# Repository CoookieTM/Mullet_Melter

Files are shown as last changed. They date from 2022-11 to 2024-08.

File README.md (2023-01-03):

# Mullet Melter (in ALPHA)

**What is the MulletMelter?**

business in the front, business in the back, party on the sides

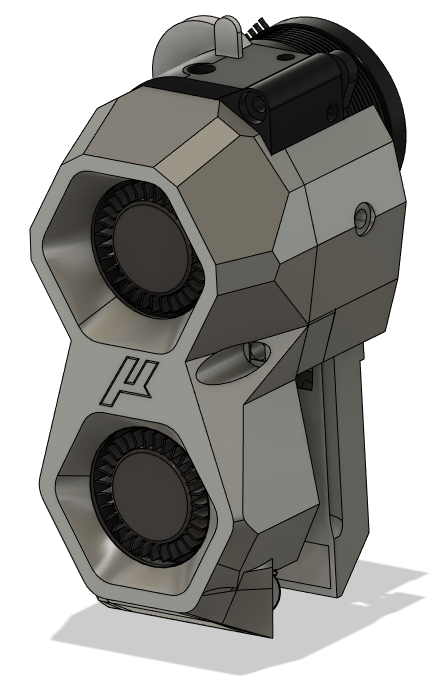
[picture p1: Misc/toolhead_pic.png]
Rendering Mullet Melter




[Join the Doomcube Discord for support under doomy-worx/Mullet_Melter](https://discord.com/channels/825469421346226226/1028744277393674290)

**Requires (3) 3010 Blower Fans**

I have 160hrs of print time on this toolhead so far. (recent toy drive haha)

<details>
    <summary>
    Hardware Required
    </summary>

Part           |Qty | Notes
 ----|----|----|
3010 Blower Fan|3 | 
m3x6		   |5 | 
m3x10 		   |4 | 
m3x10 BHCS     |2 | Must be BHCS
m3x12          |2 |
m3x8           |1 |
heatset inserts|3 |
LGx Lite       |1 |
Revo Voron     |1 |
</details>

Thanks to the following people on Discord who have helped test pre-alpha:

- @Dentox_
- @bwnance

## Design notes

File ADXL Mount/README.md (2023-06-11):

Hardware Required

Part           |Qty | Notes
 ----|----|----|
m3x30		   |1 | 
m3x40 		   |1 | 
heatset inserts|2 |
</details>

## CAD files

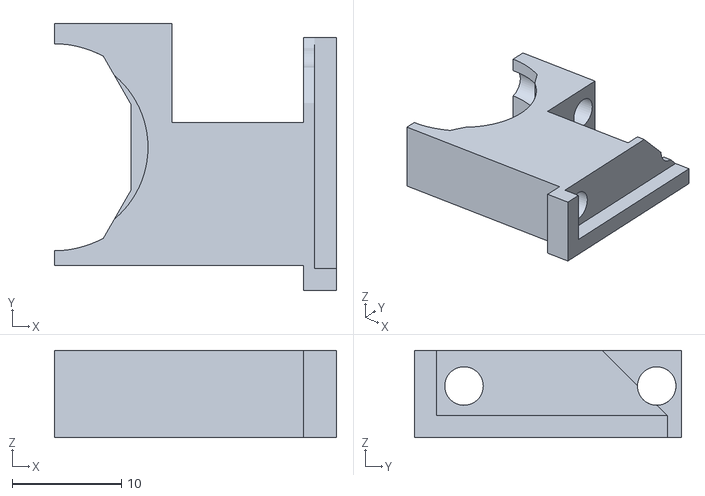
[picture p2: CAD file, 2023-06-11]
ADXL Mount/adxlmount_a.stl
25.8 x 24.4 x 7.99

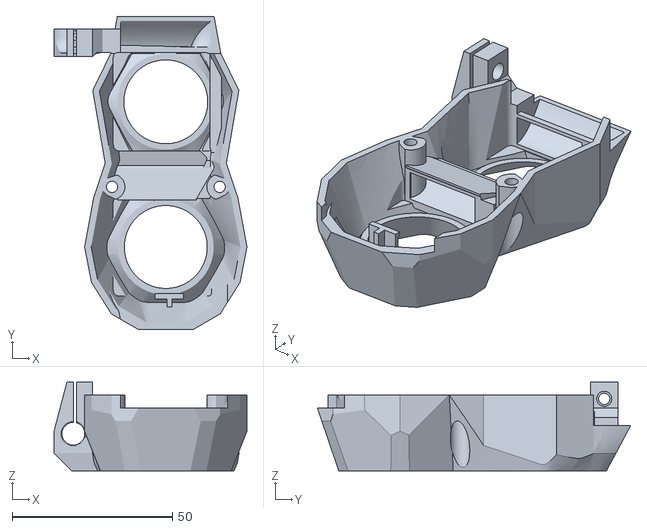
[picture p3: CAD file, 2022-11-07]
Pinda/shroud.stl
60.1 x 97.6 x 27.6

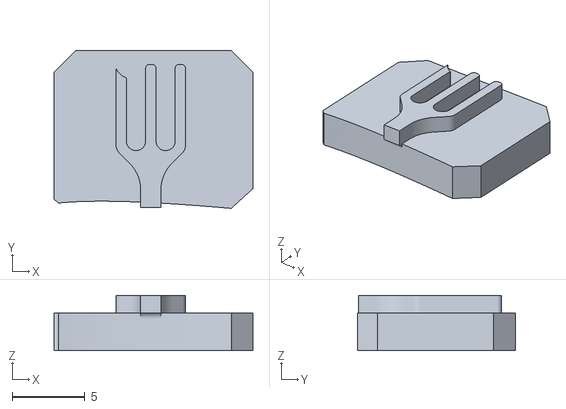
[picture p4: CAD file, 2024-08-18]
Standard/salad_fork/salad_fork_diffuser.stl
13.7 x 10.8 x 3.80

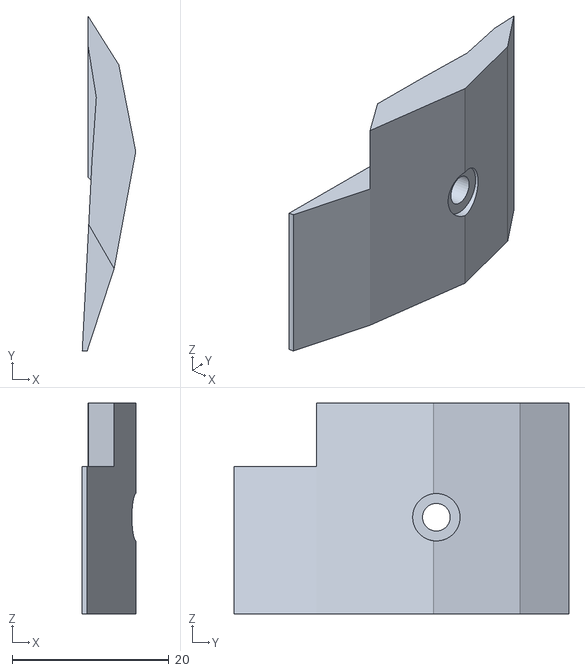
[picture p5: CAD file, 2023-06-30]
Standard/wire_cover.stl
6.83 x 42.8 x 26.9

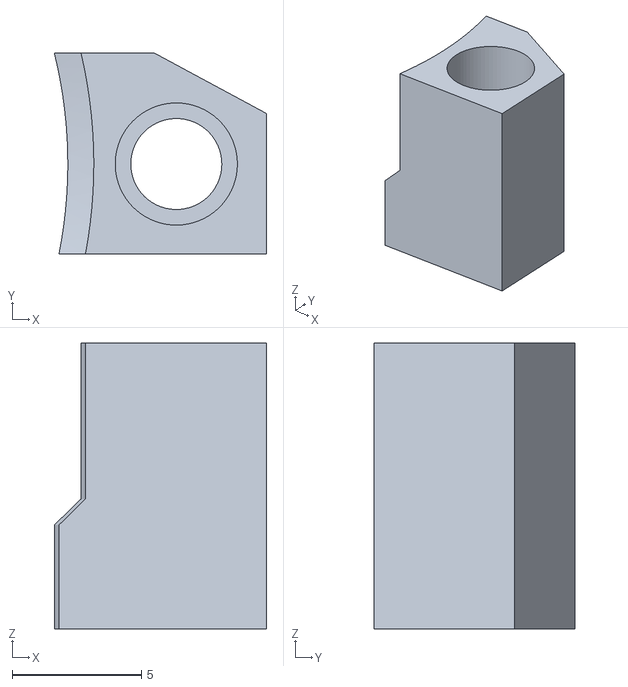
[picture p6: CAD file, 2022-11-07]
Toolhead_Board_Mount/DFH/dfh_coupler_a.stl
8.21 x 7.77 x 11.1

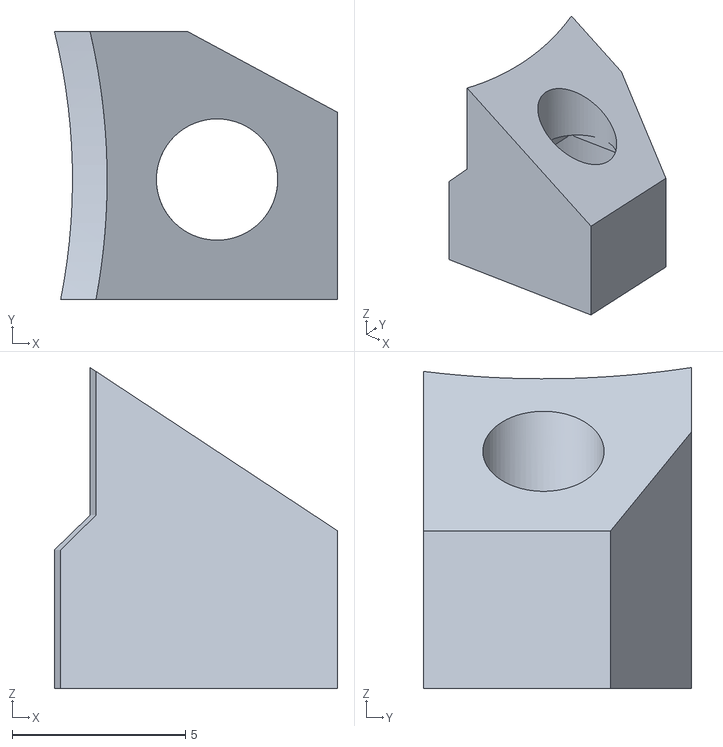
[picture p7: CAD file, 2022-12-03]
Toolhead_Board_Mount/EBB36/coupler_c.stl
8.17 x 7.73 x 9.26

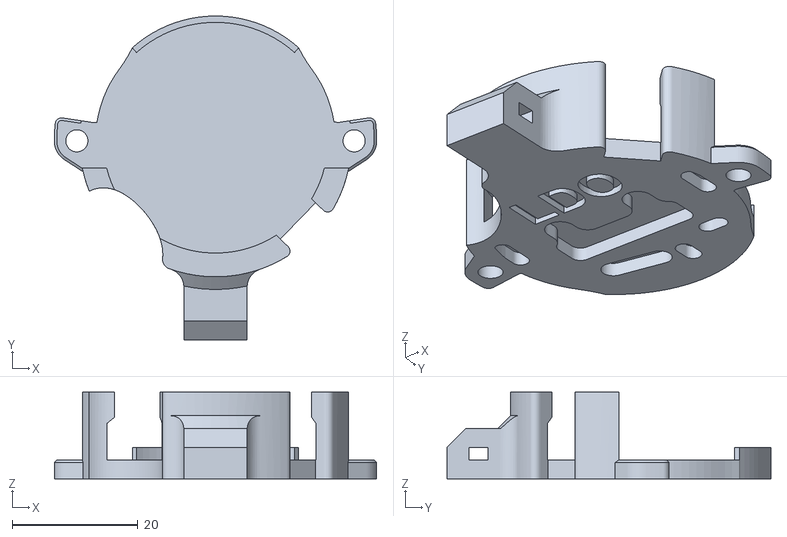
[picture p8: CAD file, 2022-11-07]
Toolhead_Board_Mount/LDO/ldo_backplate.stl
51.3 x 51.5 x 13.8

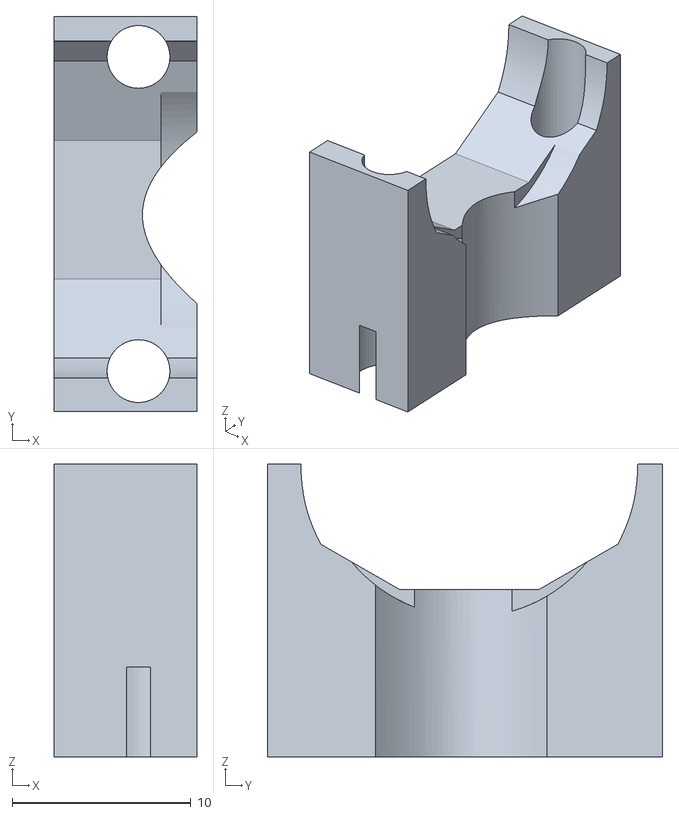
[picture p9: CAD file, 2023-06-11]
ADXL Mount/adxlmount_b.stl
7.99 x 22.1 x 16.4

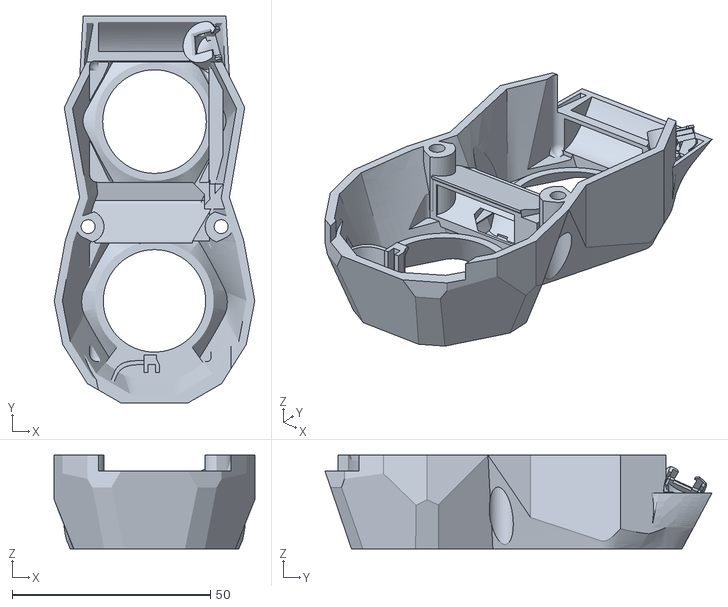
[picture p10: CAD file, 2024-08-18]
Standard/salad_fork/shroud_salad_fork.stl
50.6 x 97.6 x 23.6

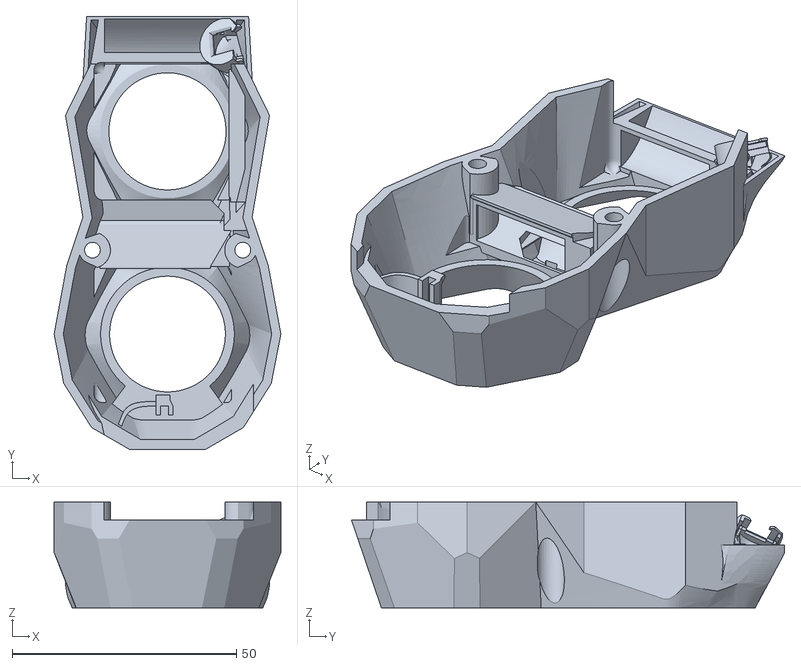
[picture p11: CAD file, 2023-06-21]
Standard/shroud.stl
50.6 x 96.6 x 23.6

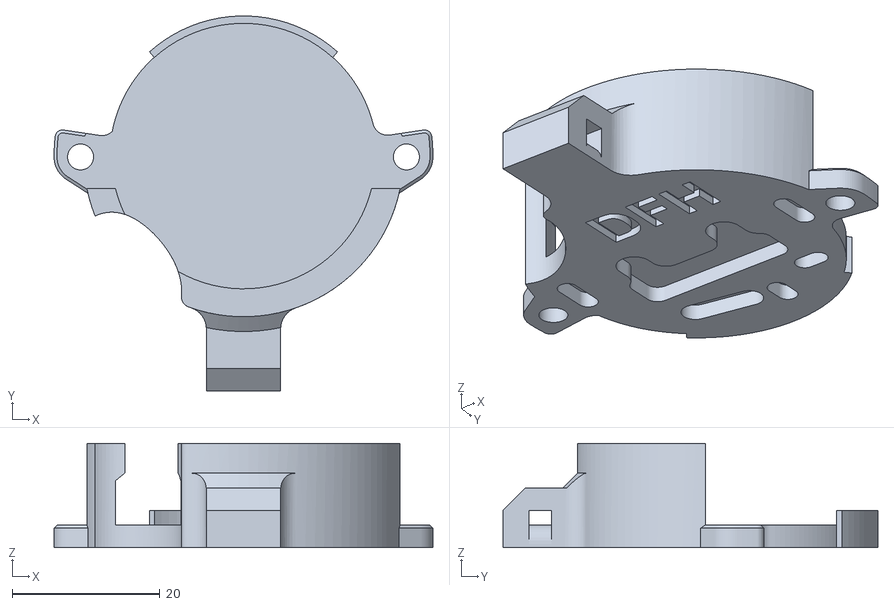
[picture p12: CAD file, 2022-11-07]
Toolhead_Board_Mount/DFH/dfh_backplate.stl
51.3 x 50.7 x 14.1

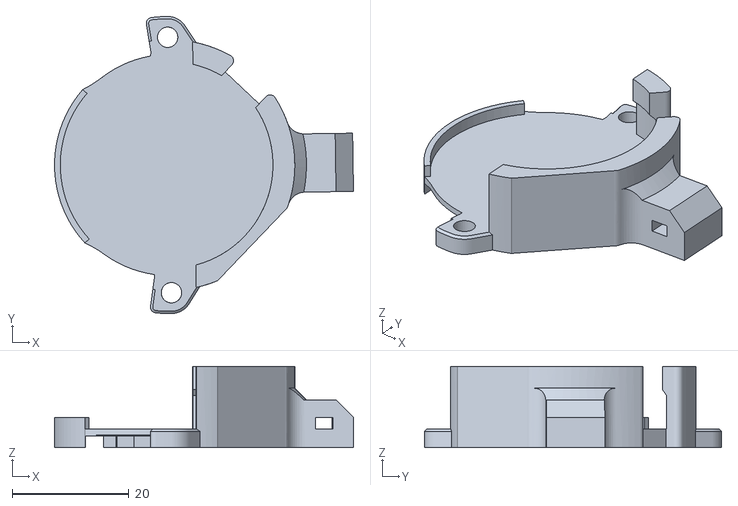
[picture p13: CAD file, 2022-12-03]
Toolhead_Board_Mount/EBB36/backplate.stl
51.3 x 51.0 x 14.0

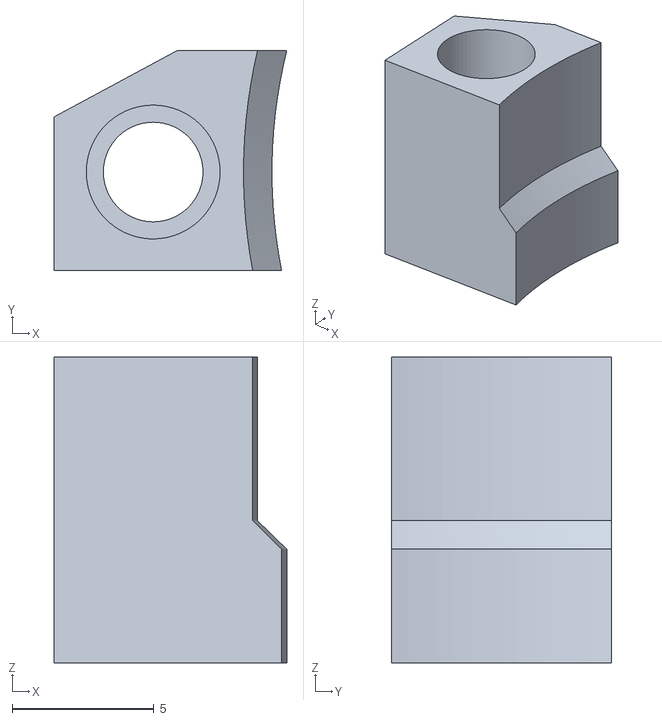
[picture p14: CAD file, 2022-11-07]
Toolhead_Board_Mount/LDO/ldo_coupler_b.stl
8.21 x 7.77 x 10.8

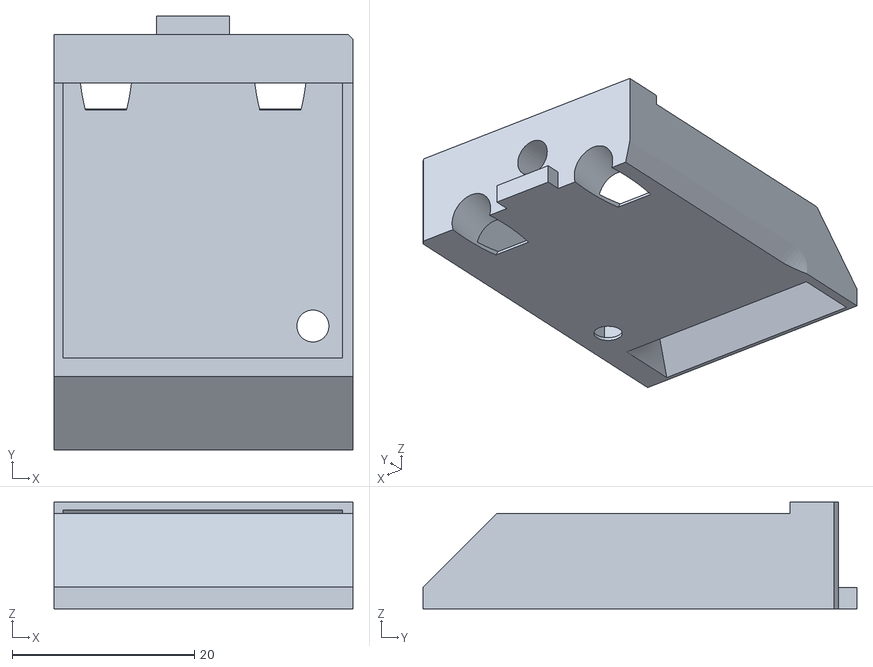
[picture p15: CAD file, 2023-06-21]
Standard/rear_fan_mount.stl
32.8 x 47.5 x 11.7

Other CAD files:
Toolhead_Board_Mount/DFH/dfh_coupler_b.stl
Toolhead_Board_Mount/EBB36/coupler_b.stl
Toolhead_Board_Mount/LDO/ldo_coupler_a.stl
Standard/micron_diffuser.stl
Standard/diffuser_holder.stl
Standard/rail_mount.stl
Toolhead_Board_Mount/EBB36/coupler_a.stl
Toolhead_Board_Mount/EBB36/coupler_d.stl

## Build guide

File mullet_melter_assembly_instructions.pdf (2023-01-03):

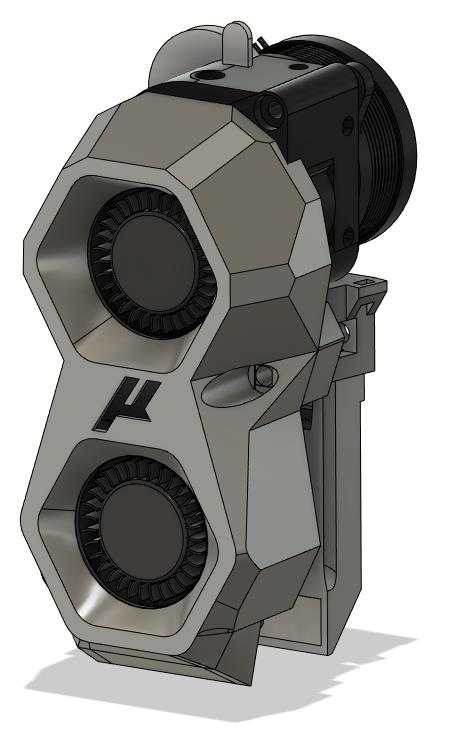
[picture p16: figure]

# Mullet Melter Assembly

### Required:

(3) 3010 Blower Fans (DFH) (https://dfh.fm/products/3010-24v-dual-ball-blower-fan?aff=3) (West3d) (https://west3d.com/products/gdstime-dc-24v-30x30x10-centrifugal-blower-fan-gdb3010-dual-ball-bearing-9500rpm-1w-05a-xh2-54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)

### LGX Lite Revo Voron or Rapido

(5) m3x6
(4) m3x10
(2) m3x10 BHCS
(2) m3x12
(1) m3x8

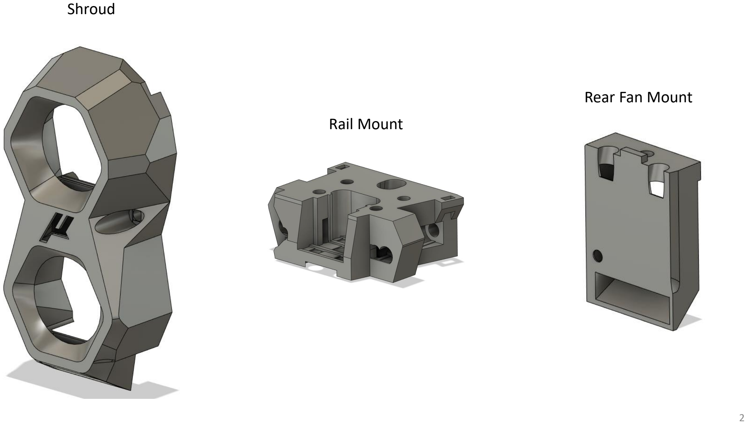
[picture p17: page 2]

Shroud

Rail Mount

Rear Fan Mount

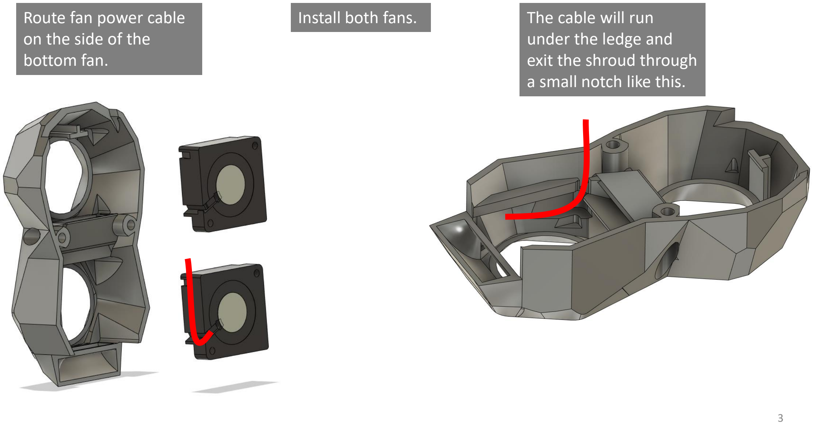
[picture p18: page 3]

Route fan power cable
on the side of the
bottom fan.

The cable will run
under the ledge and
exit the shroud through
a small notch like this.

Install both fans.

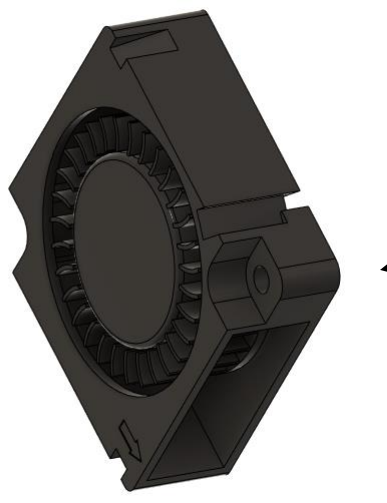
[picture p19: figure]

Use an m3x6 bolt to
pre thread this hole in
the 3010 blower.

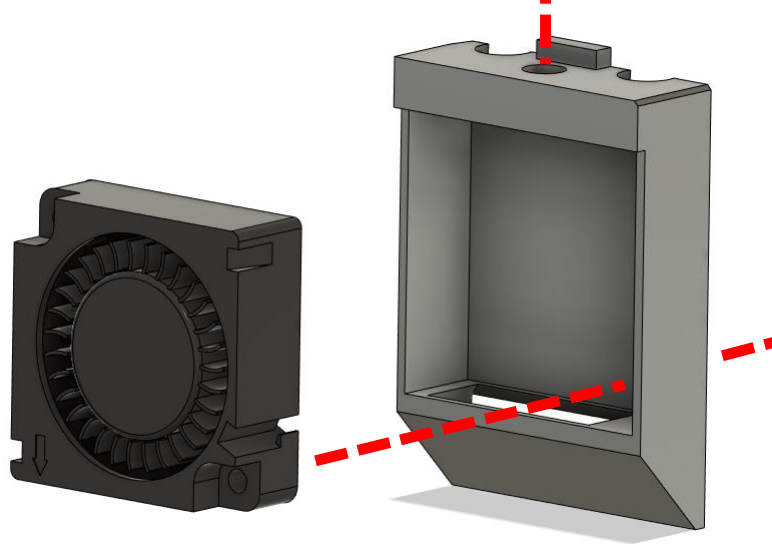
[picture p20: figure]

Remove bolt and reinstall into the rear fan
mount.

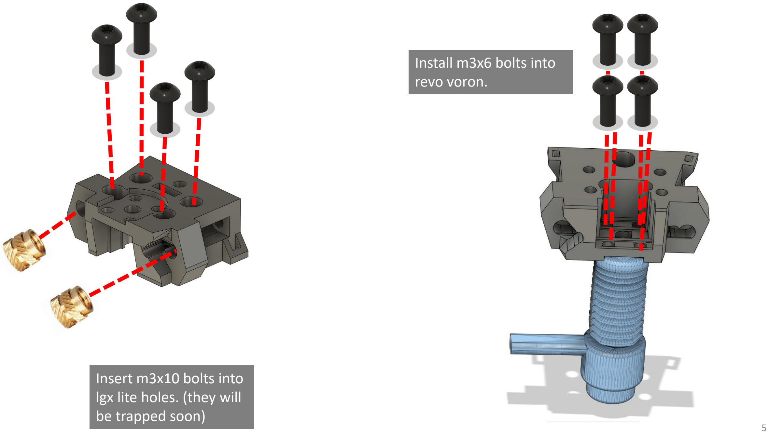
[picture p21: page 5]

Insert m3x10 bolts into
lgx lite holes. (they will be trapped soon)

Install m3x6 bolts into
revo voron.

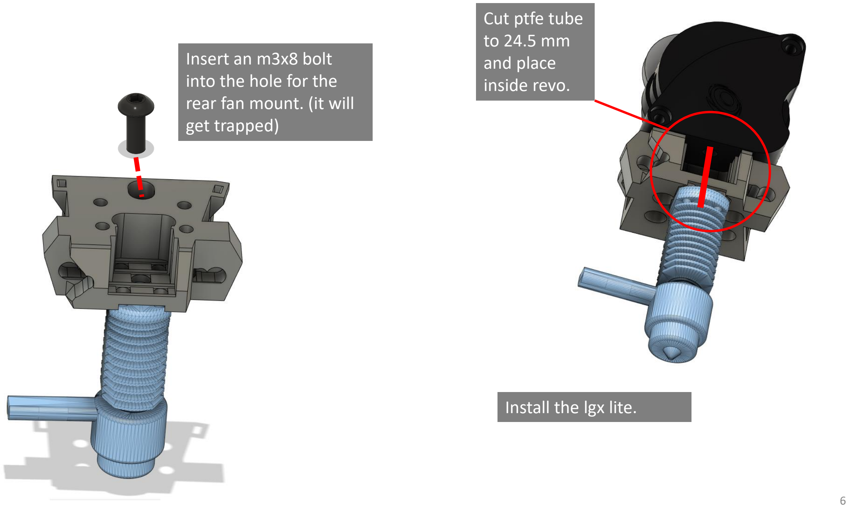
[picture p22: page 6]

Insert an m3x8 bolt
into the hole for the
rear fan mount. (it will
get trapped)

Install the lgx lite.

Cut ptfe tube
to 24.5 mm
and place
inside revo.

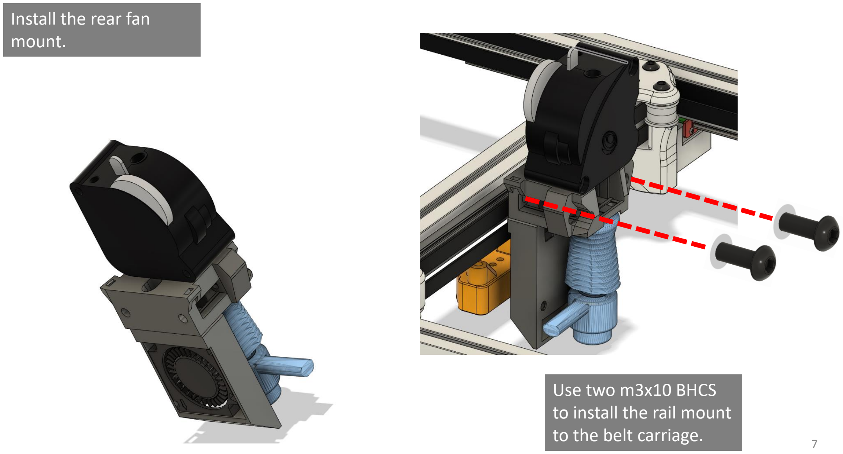
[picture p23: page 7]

Install the rear fan
mount.

Use two m3x10 BHCS
to install the rail mount
to the belt carriage. | 7

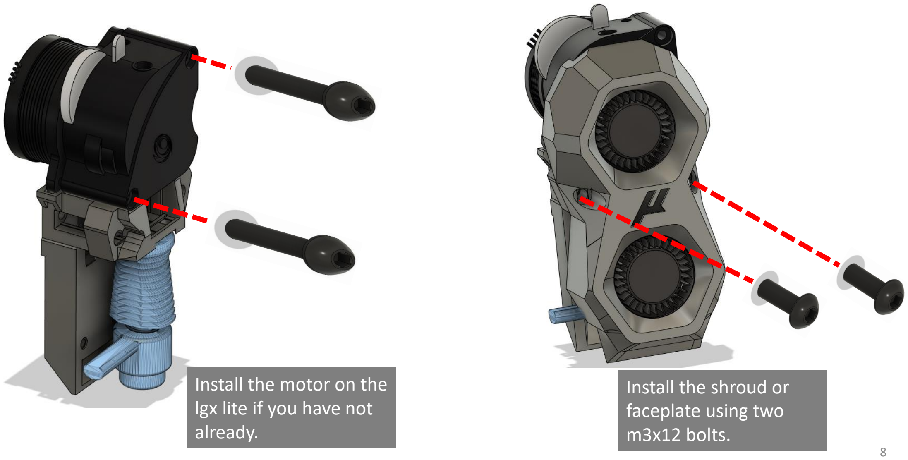
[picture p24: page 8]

Install the motor on the
lgx lite if you have not
already.

Install the shroud or
faceplate using two
m3x12 bolts.

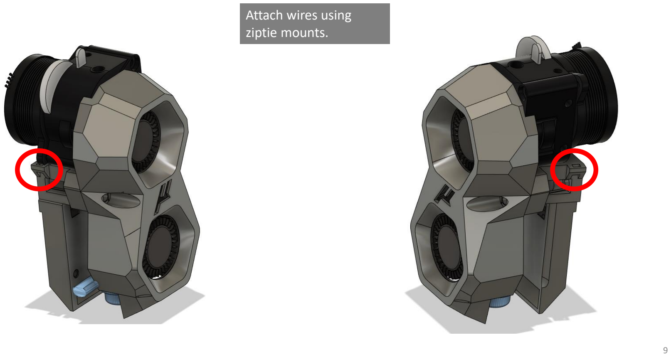
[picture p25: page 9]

Attach wires using
ziptie mounts.

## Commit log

2022-11-06 Initial commit.
    [dfh_backplate.stl, dfh_coupler_a.stl, dfh_coupler_b.stl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]
2022-11-07 Fix hole and add insert iron clearance.
    [shroud.stl]
2022-11-07 Fix abs scale and stl orientation.
    [dfh_backplate.stl, dfh_coupler_a.stl, dfh_coupler_b.stl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]
2022-11-08 Initial commit with hole fix.
    [shroud.stl]
2022-11-11 Printability QOL.
    [rail_mount.stl]
2022-11-11 Add hole for securing fan.
    [rear_fan_mount.stl]
2022-11-18 Add ptfe tube.
2022-12-03 Add print time.
2022-12-03 Add EBB36 support.
    [backplate.stl, coupler_a.stl, coupler_b.stl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]
2023-01-03 Add PTFE tube length.
2023-03-25 Add LED logo and nozzle support. (Alpha 2)
    [diffuser_holder.stl, micron_diffuser.stl, shroud.stl]
2023-06-11 add adxl mount
    [adxlmount_a.stl, adxlmount_b.stl]
2023-06-21 shave off 1mm for easier/safer z end stop homing
    [rear_fan_mount.stl, shroud.stl]
2023-06-30 Add wire cover.
    [wire_cover.stl]
2024-08-18 Edit shroud and LED diffuser for SF logo
    [salad_fork_diffuser.stl, shroud_salad_fork.stl]
